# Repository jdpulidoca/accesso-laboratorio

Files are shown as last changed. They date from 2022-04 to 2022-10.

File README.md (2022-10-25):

# Proyecto Sistemas Embebidos 2022-1 : Control de Acceso para Laboratorios

## Brochure

<p align="center">
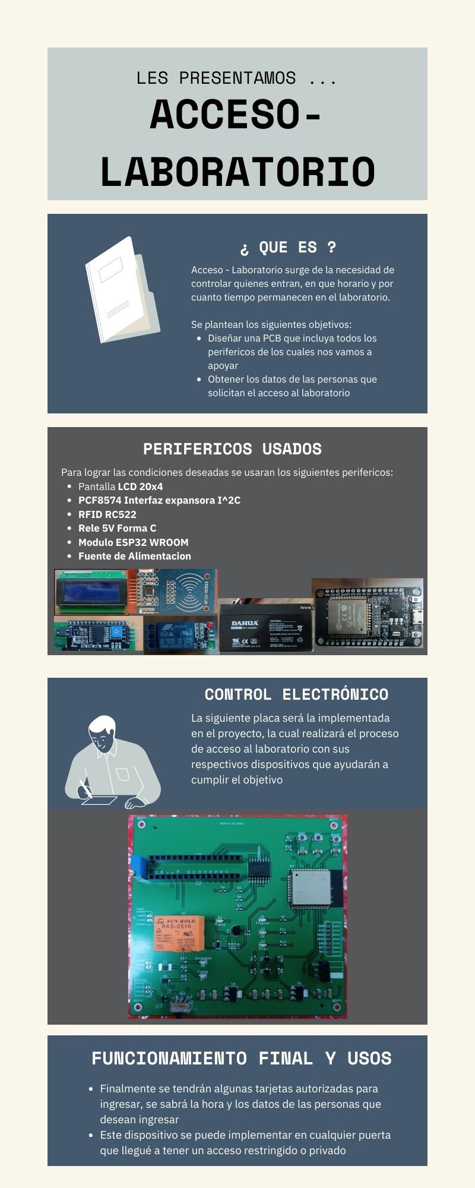
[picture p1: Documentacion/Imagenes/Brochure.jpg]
  
</p>

## Descripción
Como primer idea se plantea un sistema para acceder a un laboratoiro. Se tienen como condiciones que el acceso sea por medio del carnet universitario, donde al acercar el carnet al dispositivo que se diseñara, este desbloqueará la puerta y mostrara los datos en pantalla de la persona que desea ingresar al laboratorio. Este dispositivo activara y desactivara un electroiman que será el encargado de mantener la puerta bloqueada.

## Desarrollo y modelamiento

### Planteamiento Base del Diseño
Para lograr el objetivo del proyecto se plantean las primeras ideas en cuanto a diseño del dispositivo, se plantean las primeras ideas basicas en forma grafica con el fin de ordenar y establecer como  distribuir las tareas que corresponde a Hardware y Software. Esta ideacion esta sujeta a cambios o ajuste debido a las limitaciones del mismo.

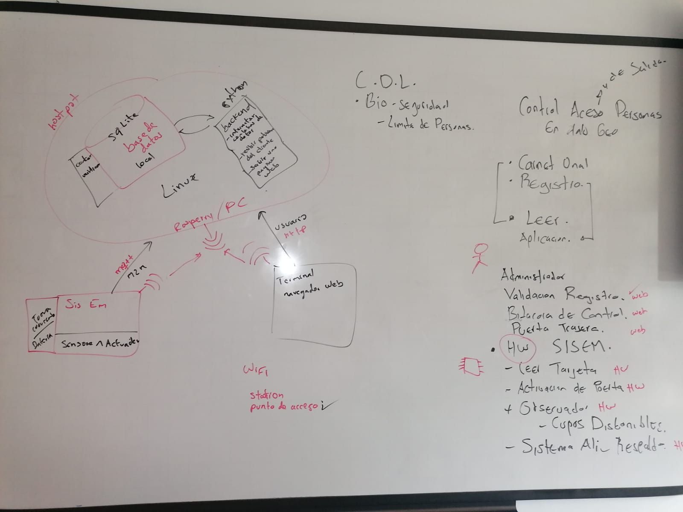
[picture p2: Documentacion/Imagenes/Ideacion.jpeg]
IdeasBasicas


### Diagrama de Bloques

<p align="center">
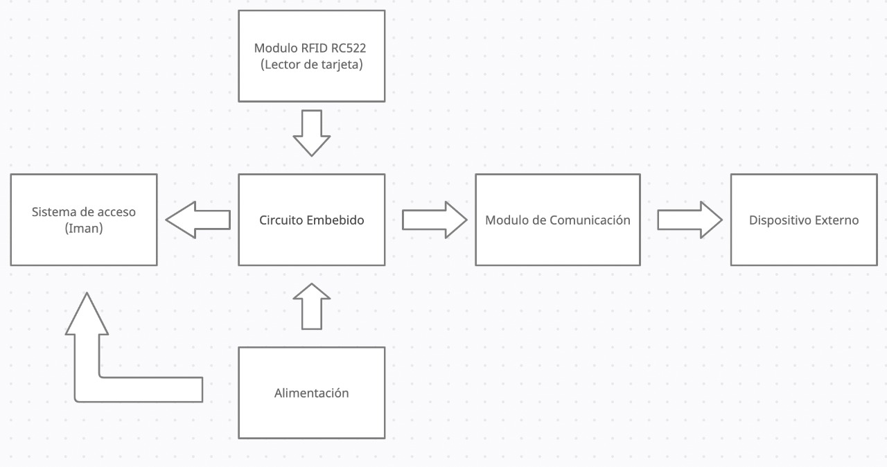
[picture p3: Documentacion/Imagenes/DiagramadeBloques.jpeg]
  
</p>

### Diagrama de Flujo

<p align="center">
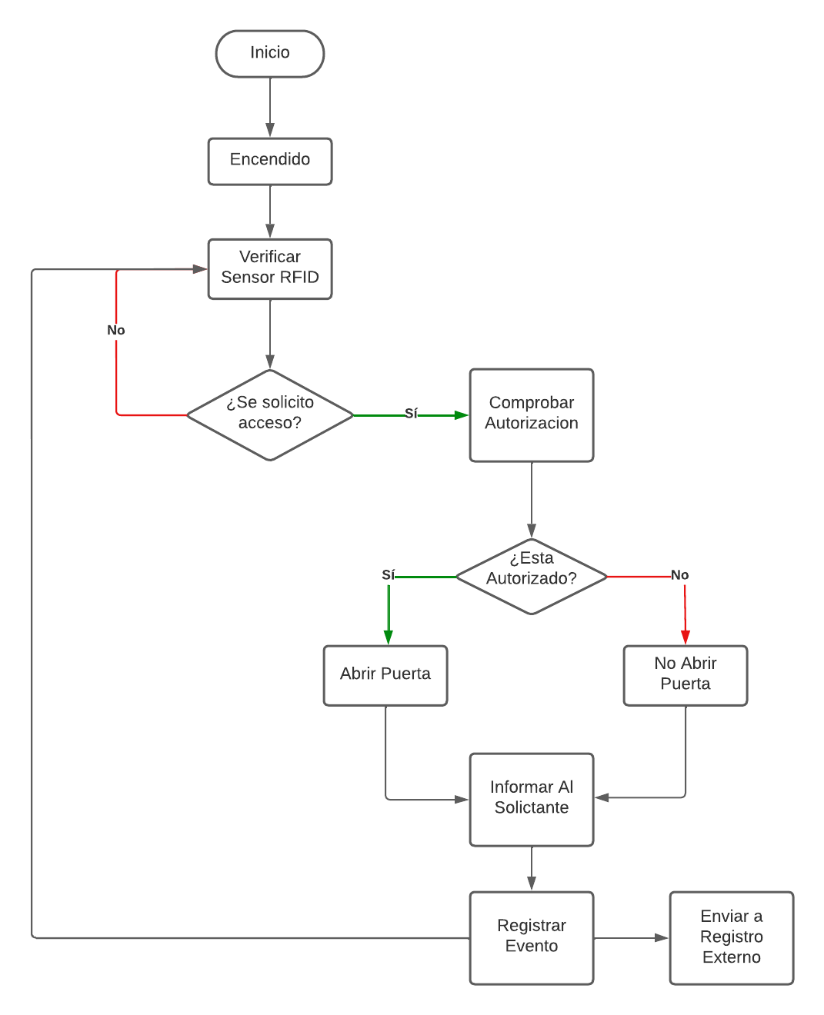
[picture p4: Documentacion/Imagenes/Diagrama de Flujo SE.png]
  
</p>

### Particionamiento Hardware y Software
#### HardWare
Para esta sección se establecen los siguientes periféricos:  
##### LCD 20x4
EL fin de este periferico es ver la información de la tarjeta con la que se desea ingresar, de igual manera ver si la solicitude de acceso al laboratoirio se aprueba o se denega.

<p align="center">
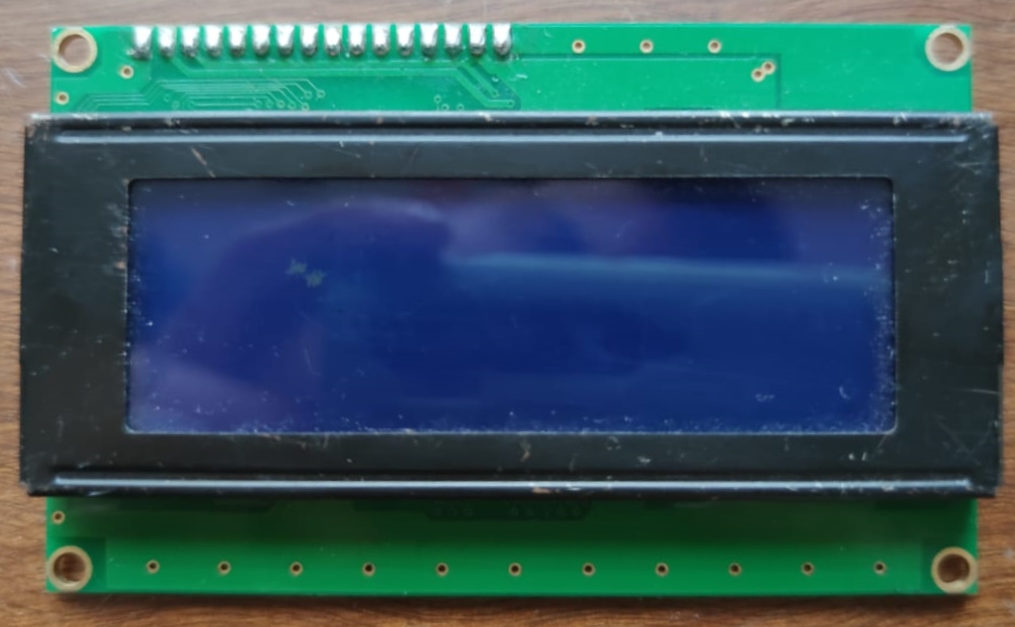
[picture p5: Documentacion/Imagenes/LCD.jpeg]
  
</p>

##### PCF8574 Interfaz expansora I^2C
Este modulo se estableció con el fin de generar una comunicación y así verificar los datos obtenidos por medio de la tarjeta entre el sistema implementado y un dispositivo externo.

<p align="center">
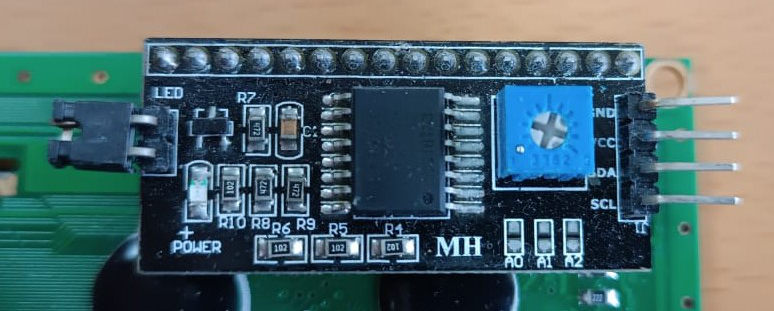
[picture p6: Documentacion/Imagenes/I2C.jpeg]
PCF8574
  
</p>

##### RFID RC522

Este modulo se implementa con el fin de leer los datos aportados por la tarjeta

<p align="center">
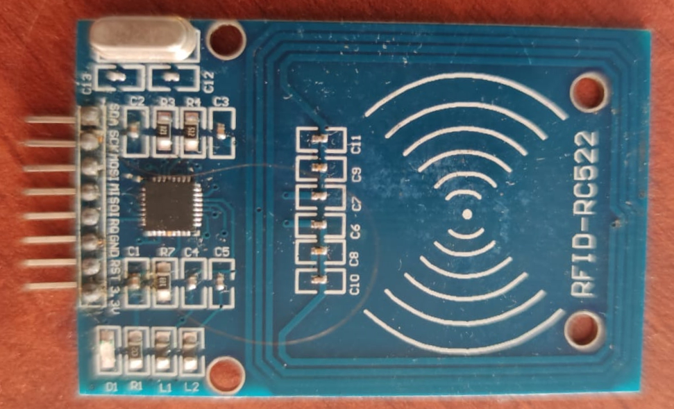
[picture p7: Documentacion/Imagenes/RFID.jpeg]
Sensor RFID-RC522
  
</p>

##### Rele 5V Forma C

Este modulo se implementa para aislar la señal digital que nos da o nos niega el acceso de la puerta

<p align="center">
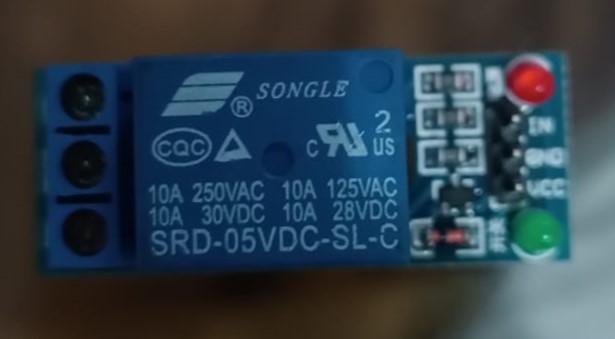
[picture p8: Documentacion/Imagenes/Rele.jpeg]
Modulo Rele 5V
  
</p>

##### Modulo ESP32 WROOM

Como último se tiene la tarjeta ESP32 desde donde se controlan los demás modulos, se implementa el codigo referente al proyecto

<p align="center">
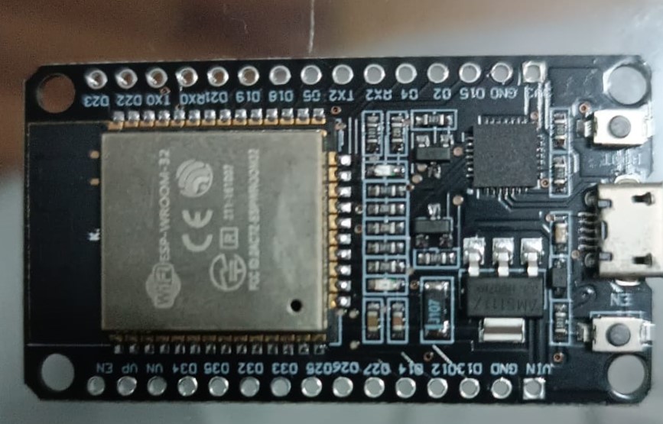
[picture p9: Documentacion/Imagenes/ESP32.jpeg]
Dev-Kit ESP32
  
</p>

##### Fuente de Alimentacion

Se plantean 2 soluciones para la alimentación del sistema, como primer solución se tiene una fuente variable que corresponde al de la siguiente imagen.

###### Fuente 12 V

<p align="center">
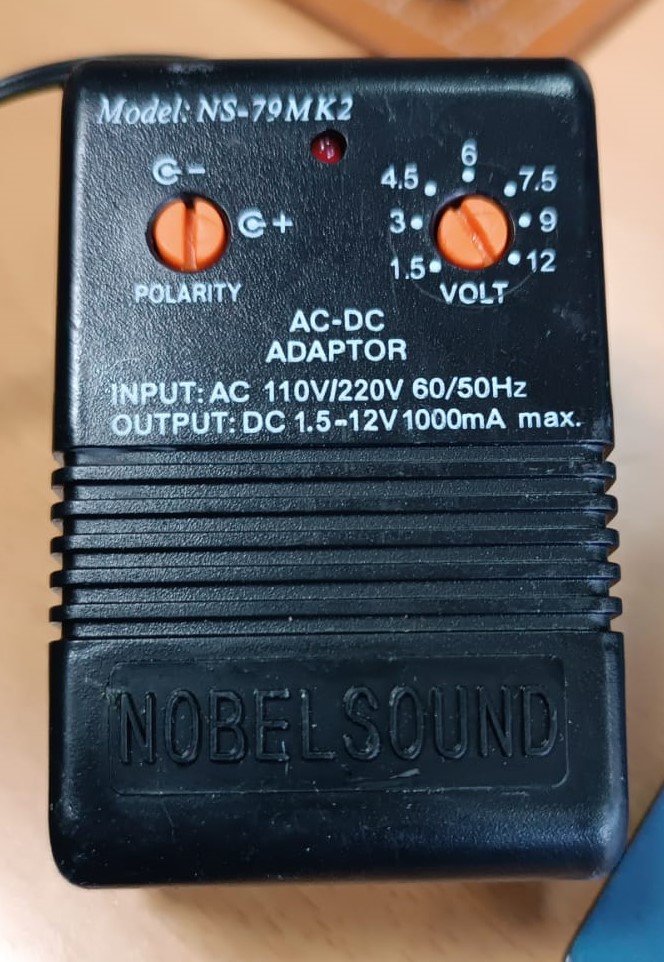
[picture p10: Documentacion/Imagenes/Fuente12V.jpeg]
Fuente12V
  
</p>

###### Bateria 12 V

Como segunda solución se plantea la implementación de una bateria extraida de una motocicleta, la cual se puede ver en la siguiente imagen

<p align="center">
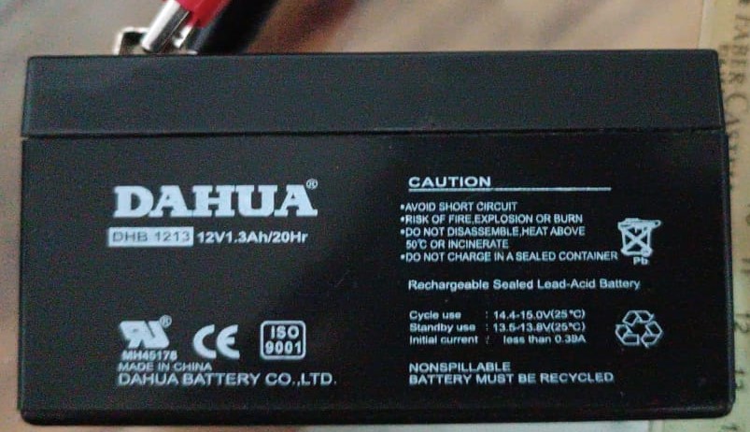
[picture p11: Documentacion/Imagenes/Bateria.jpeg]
Bateria 12 V
  
</p>

#### SoftWare
##### Codigo

### Esquema del Diseño

Este se divide en 4 "Islas" principales, divididos segun los valores de alimentacion. 

En primera instancia se se tienen los componetes que operan a con 3.3 V

En la siguiente imagen se muestra las conecciones a la ESP32, puertos de programación y adicional a esto tambien se puede evidenciar las conecciones del modulo RFID

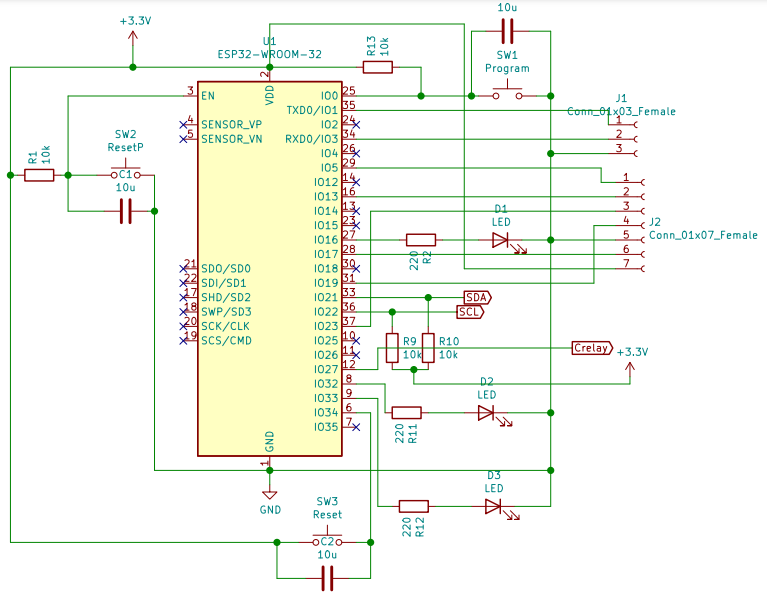
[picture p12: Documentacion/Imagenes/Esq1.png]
Esq1


Para la siguiente imagen se tienen las conecciones correspondientes a I2C para las pantallas LCD

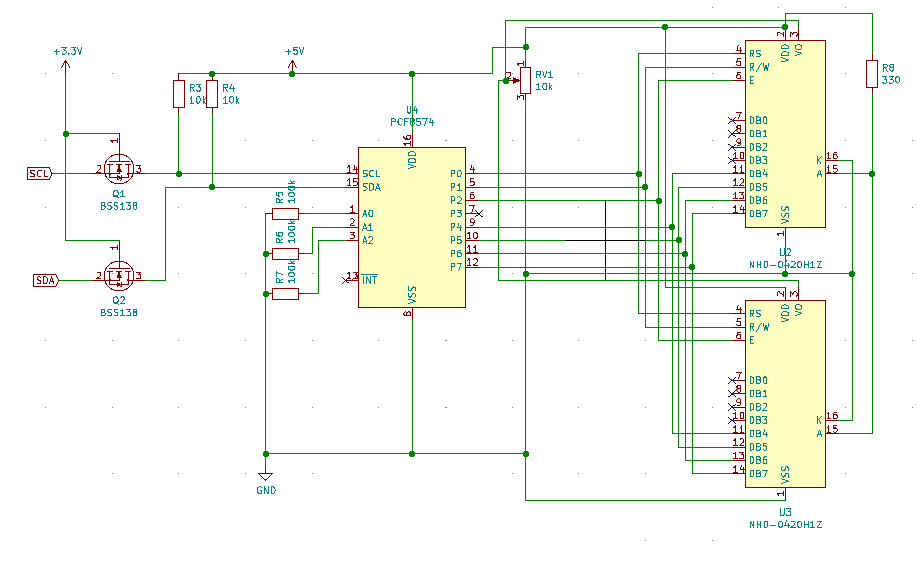
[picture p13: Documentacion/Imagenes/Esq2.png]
Esq2


Coneccion del rele con su respectivo controlador con el fin de activarlo con 3.3v y dar acceso al sistema

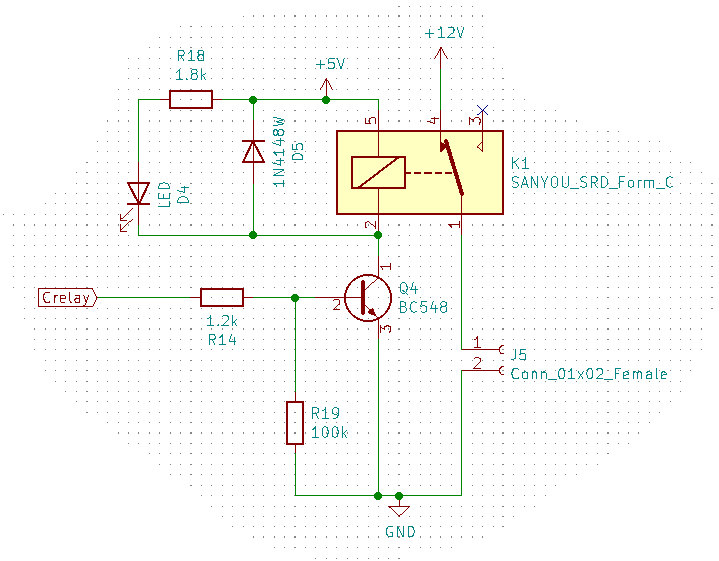
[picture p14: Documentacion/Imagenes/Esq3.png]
Esq3


Y por ultimo tenemos un sistema de fuentes lineales con el cual podemos reducir la tensión de 12v a 5v y de 5v a 3.3. Este mismo cambio de fuente a bateria en caso de una interrupción en la alimentación

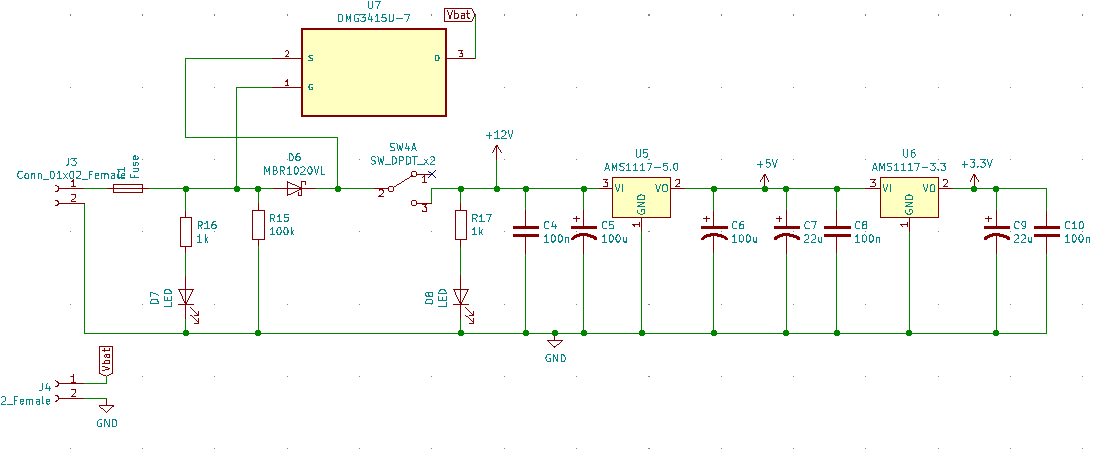
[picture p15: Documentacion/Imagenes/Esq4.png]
Esq4


### Diseño del Circuito Impreso

Se muestra el prototipo que se obtendra al imprimir la tarjeta y los dispositivos a soldar

<p align="center">
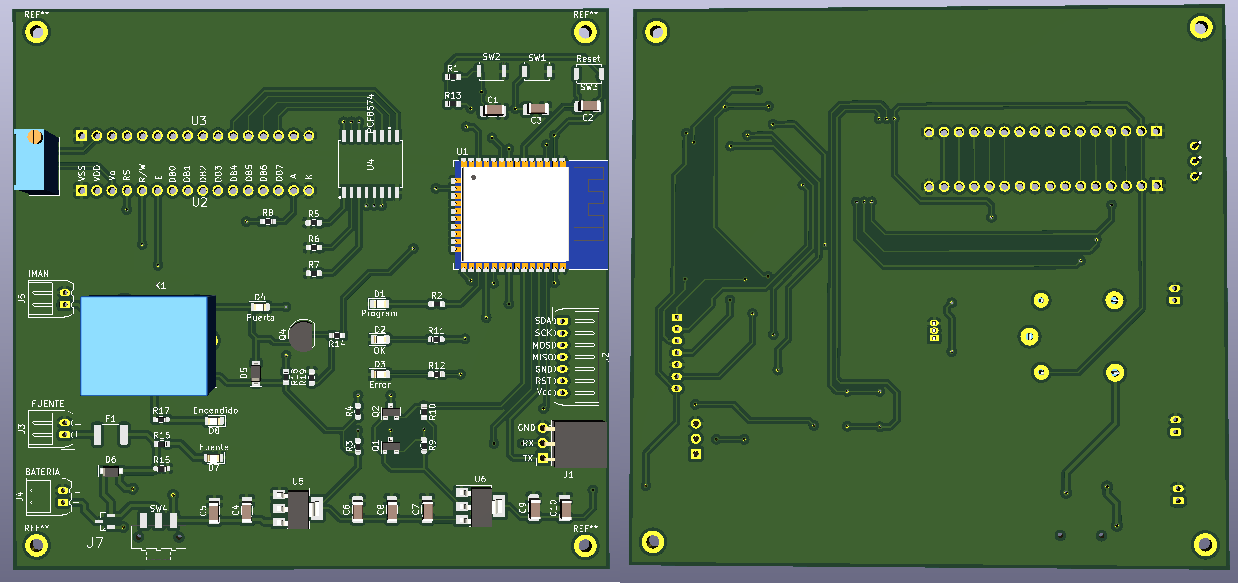
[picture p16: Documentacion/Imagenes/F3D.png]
  
</p>

### Error de Diseño
### Proceso de Compra

Despues de terminar el diseño de la PCB se empieza a estuiar los posibles proveedores para mandar imprimir dicha placa, con lo que se decide mandarla imprimir en JLCPBC

<p align="center">
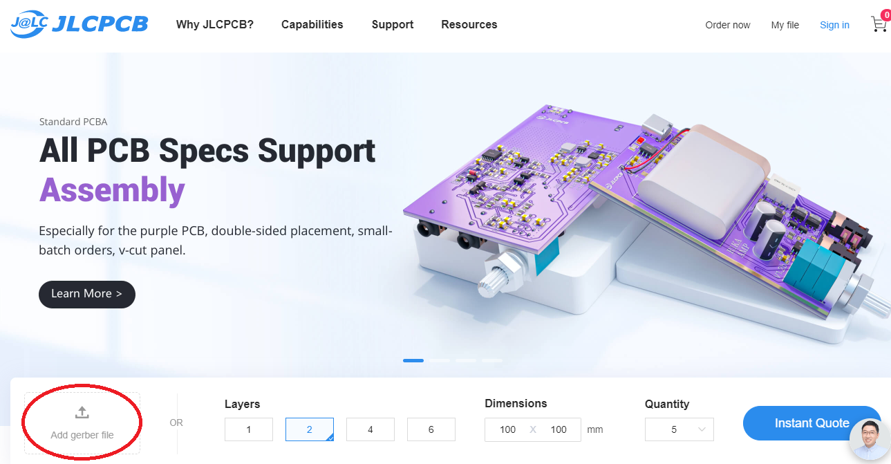
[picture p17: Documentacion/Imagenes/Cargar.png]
  
</p>

Seguido a esto se carga el diseño y se confirma la compra, la compra se realiza con tarjeta de debito.

En las siguientes imagenes se observara el proceso de compra paso a paso

Se seleccionan las diferentes caracteristicas referentes a la PCB y a los datos de envio, tambien se evidencian los costos e impuestos adicionales que no se tenían previstos.
<p align="center">
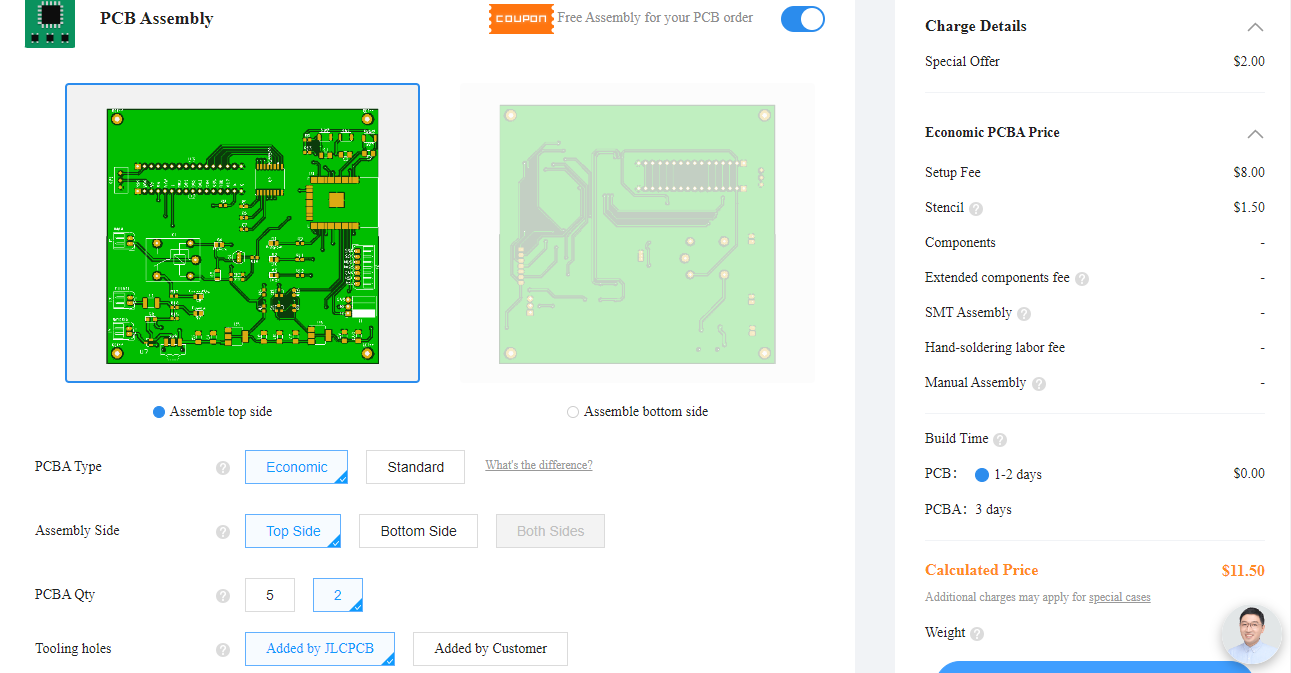
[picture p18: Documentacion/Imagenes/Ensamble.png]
  
</p>

Datos de envio
<p align="center">
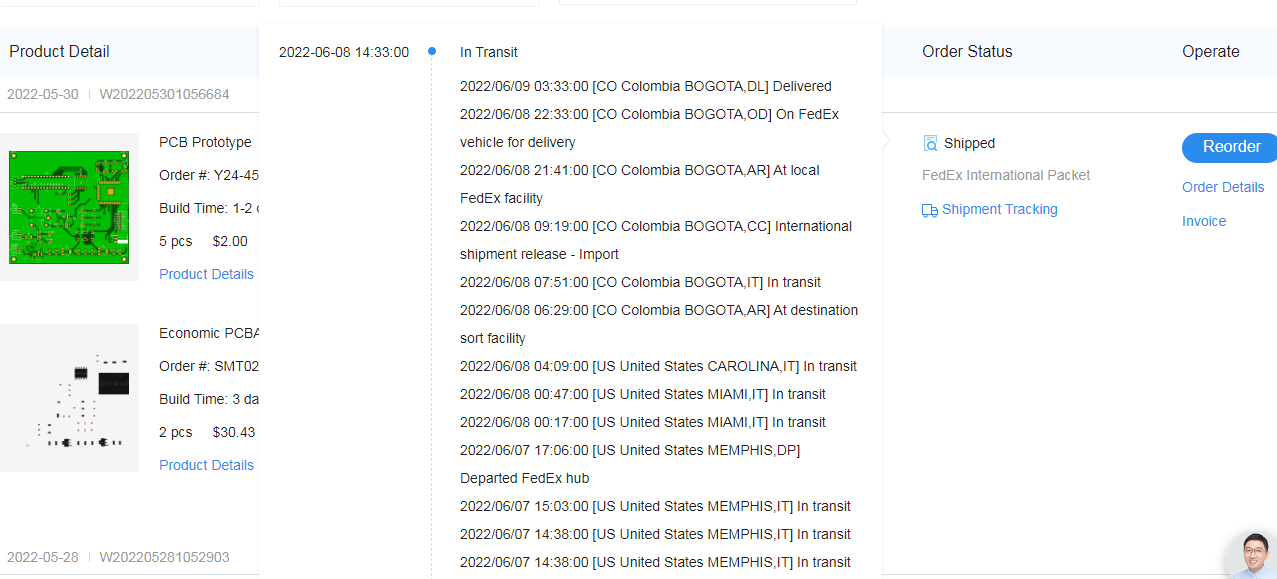
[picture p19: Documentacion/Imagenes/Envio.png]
  
</p>

Valor estimado

<p align="center">
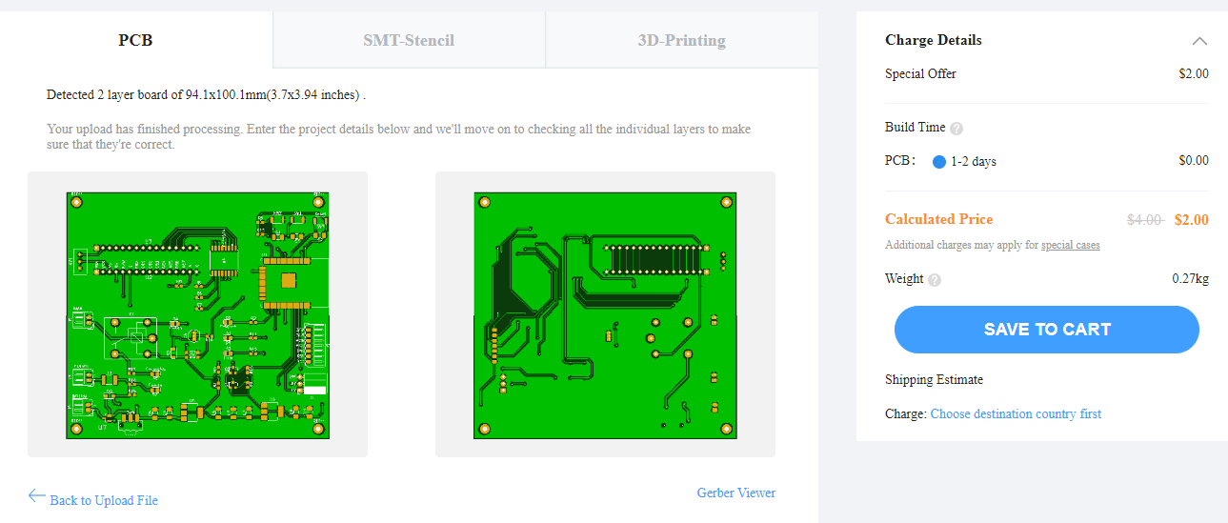
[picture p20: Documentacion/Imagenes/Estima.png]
  
</p>

Se modifica el archivo de elementos que se solicitaron soldar ya que la pagina solicitaba un formato especifico para poder ser procesado. Adicional a esto se escogen los dispositivos donde se tratan de adecuar a la necesidad del proyecto y al presupuesto

<p align="center">
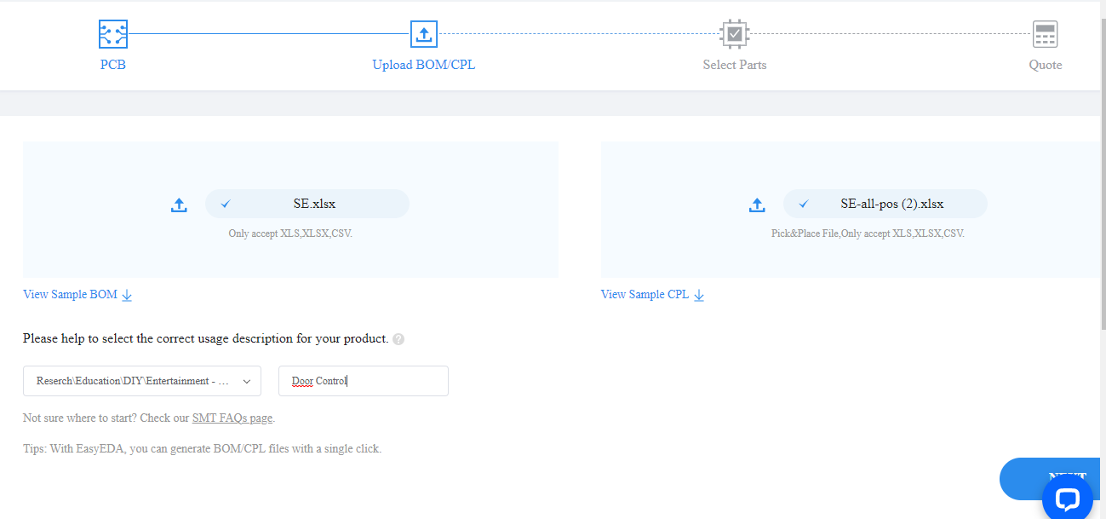
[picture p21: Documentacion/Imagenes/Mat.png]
  
</p>

<p align="center">
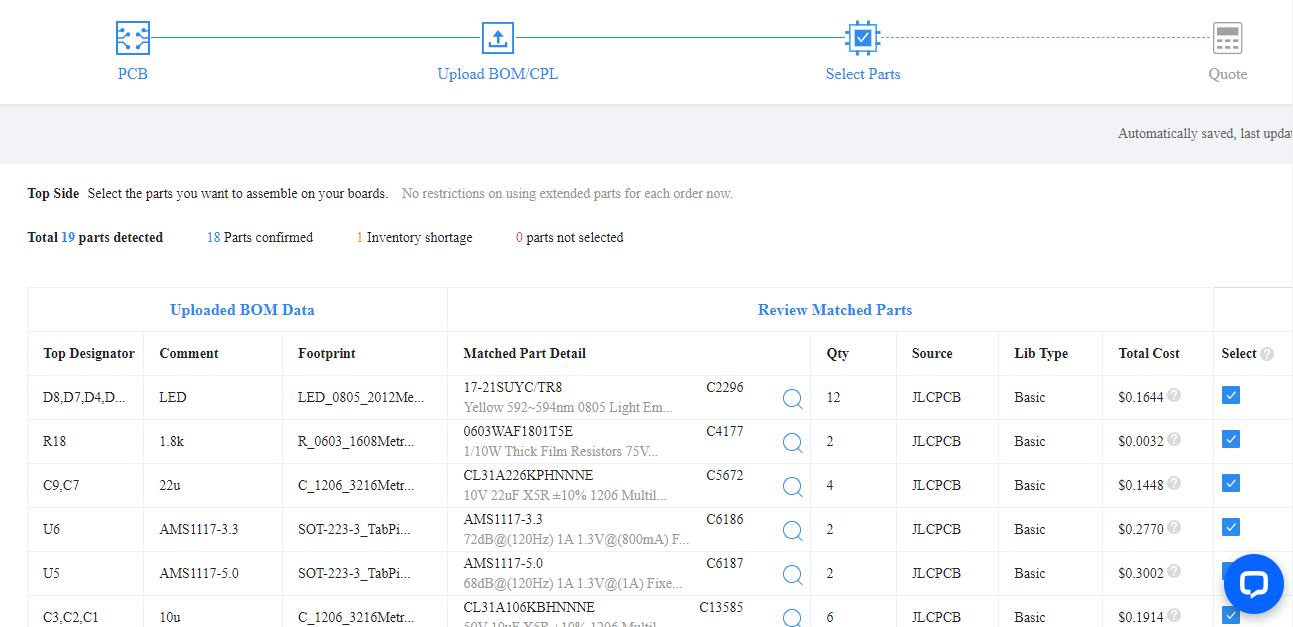
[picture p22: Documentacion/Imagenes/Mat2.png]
  
</p>

<p align="center">
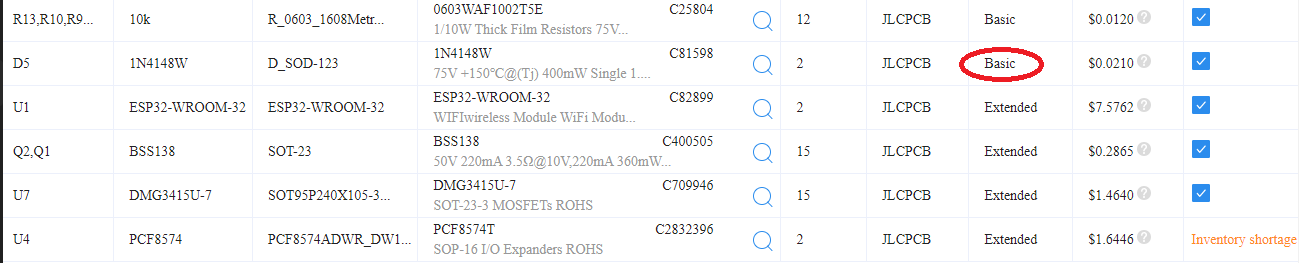
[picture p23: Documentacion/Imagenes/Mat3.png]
  
</p>

Se adjunta evidencia del proceso de compra

<p align="center">
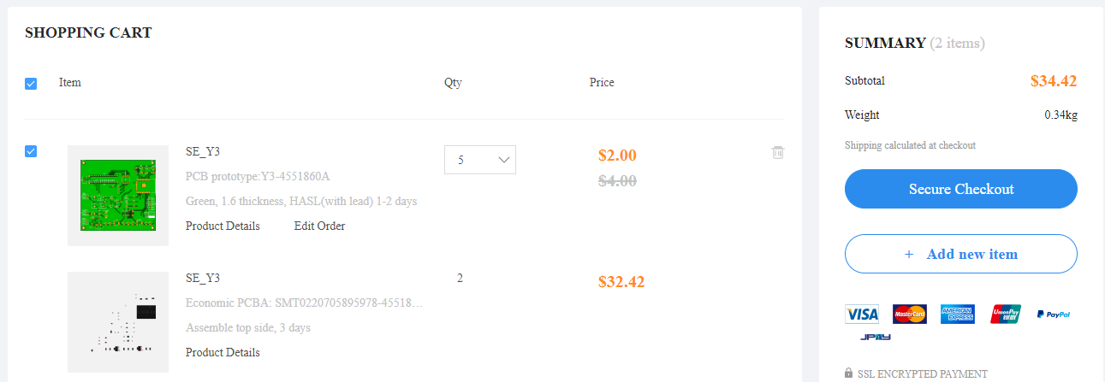
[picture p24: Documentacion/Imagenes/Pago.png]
  
</p>
<p align="center">
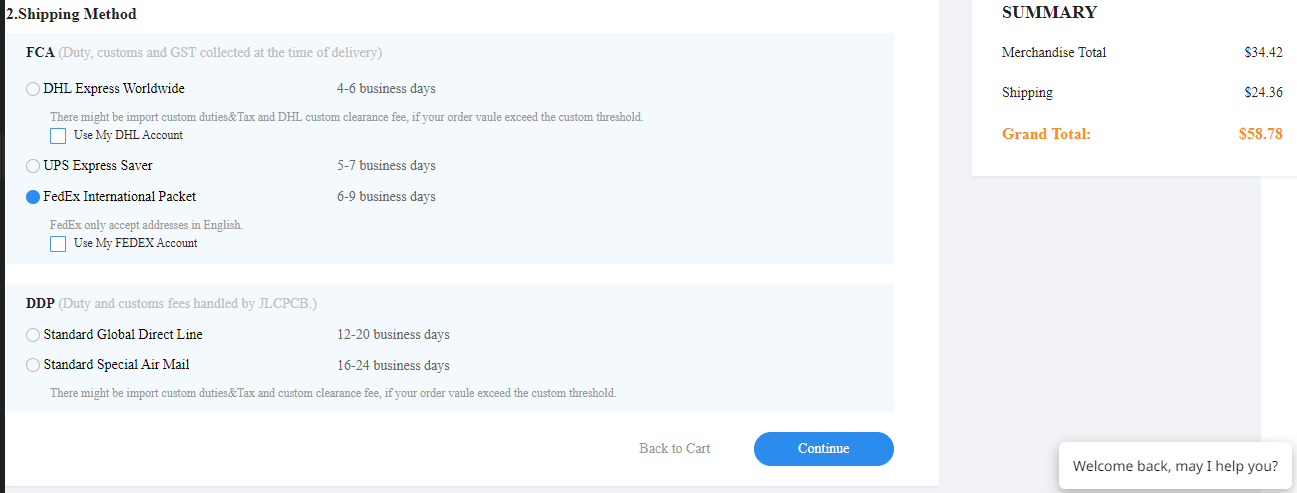
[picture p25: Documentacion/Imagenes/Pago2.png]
  
</p>

<p align="center">
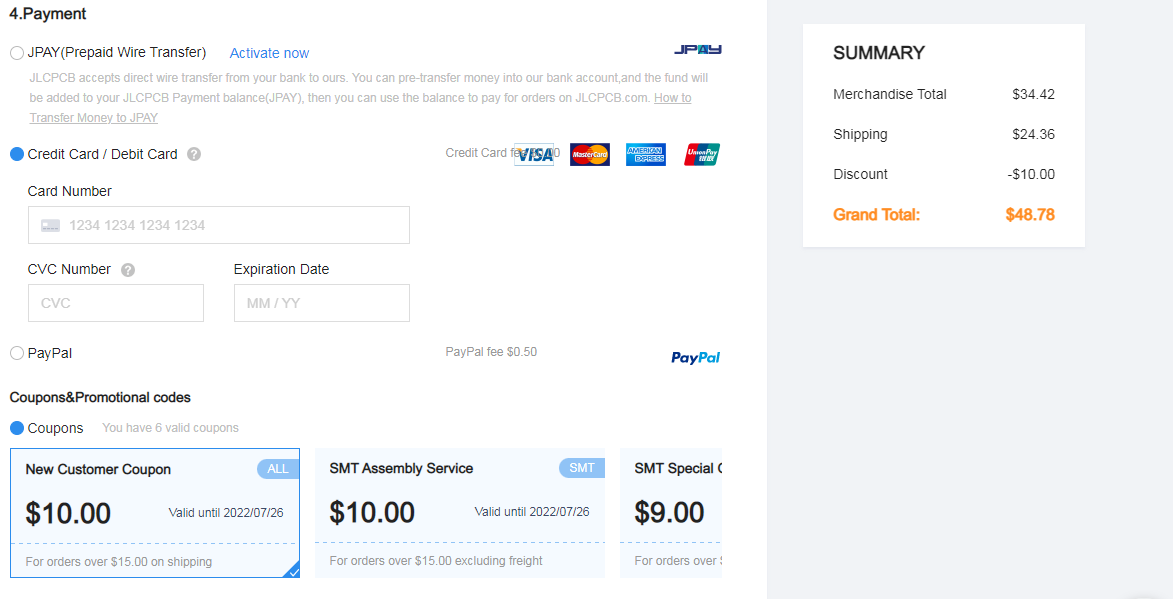
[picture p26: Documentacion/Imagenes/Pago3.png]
  
</p>

Se muestra la factura del impuesto adicional que toca pagar al llegar el paquete. este impuesto se entiende como un proceso de nacionalización del producto ya que Colombia no posee tratado de libre comercio con china.

<p align="center">
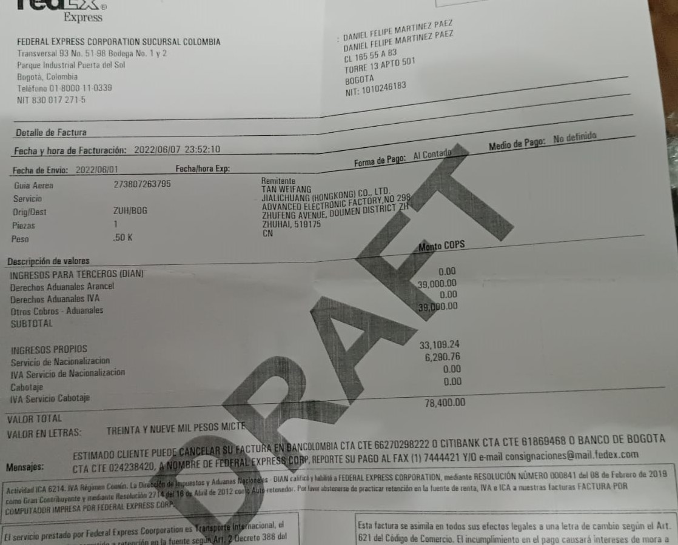
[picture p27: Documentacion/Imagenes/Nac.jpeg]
  
</p>

<p align="center">
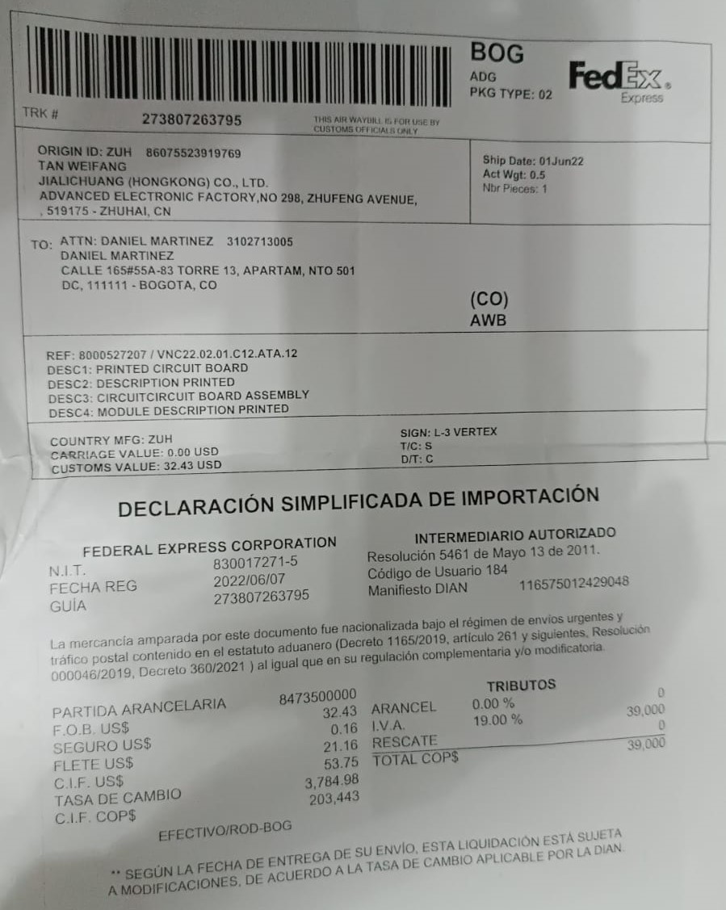
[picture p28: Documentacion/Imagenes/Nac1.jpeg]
  
</p>

## Pruebas
Las pruebas se realizaron sobre 2 tajetas. En primer lugar se trabajo con una tarjeta  experimental, que consiste en una baquelita solda donde se probaron los perifericos mediantes una tarjeta de desarrollo ESP32 DEVKIT V1. Una vez comprobado el funcionamiento de los perifericos y el codigo en la tarjeta experimental, se procede a aplicarlo en la PCB diseñada y realizar los cambios pertinentes para lograr las tares que se requieren.
### Experimental

Primero se prueban cada uno de los perifericos con el fin de verificar que esten en buen estado como se muestran en las siguientes imagenes

Empezamos adecuando un ESP32 para hacer las pruebas
<p align="center">
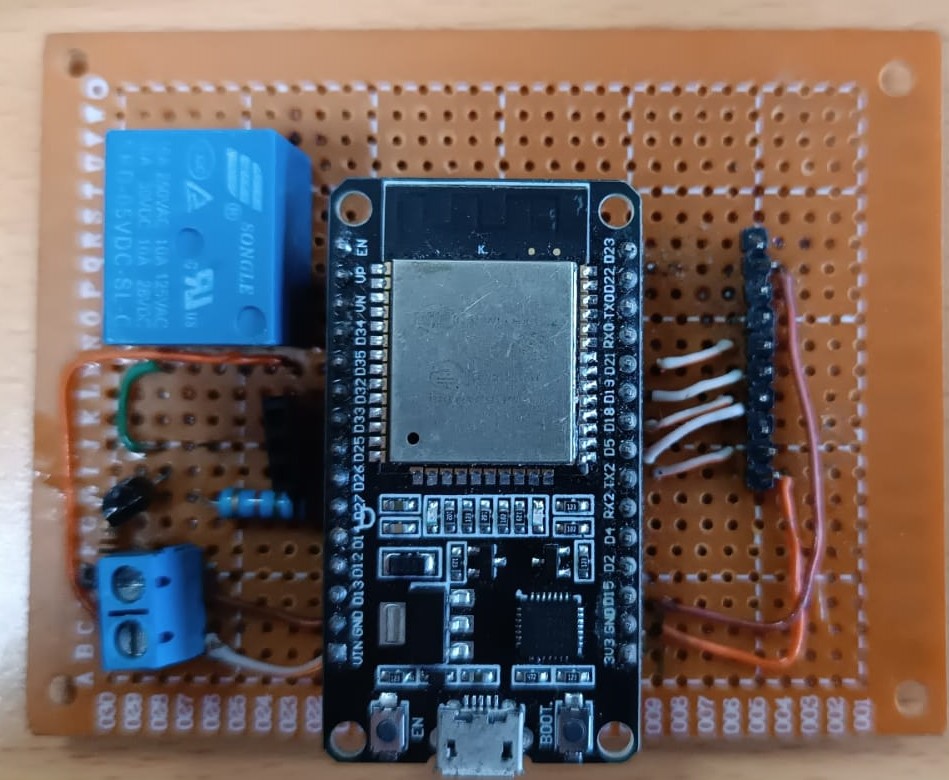
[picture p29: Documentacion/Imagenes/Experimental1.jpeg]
Tarjeta EXperimental
  
</p>
<p align="center">
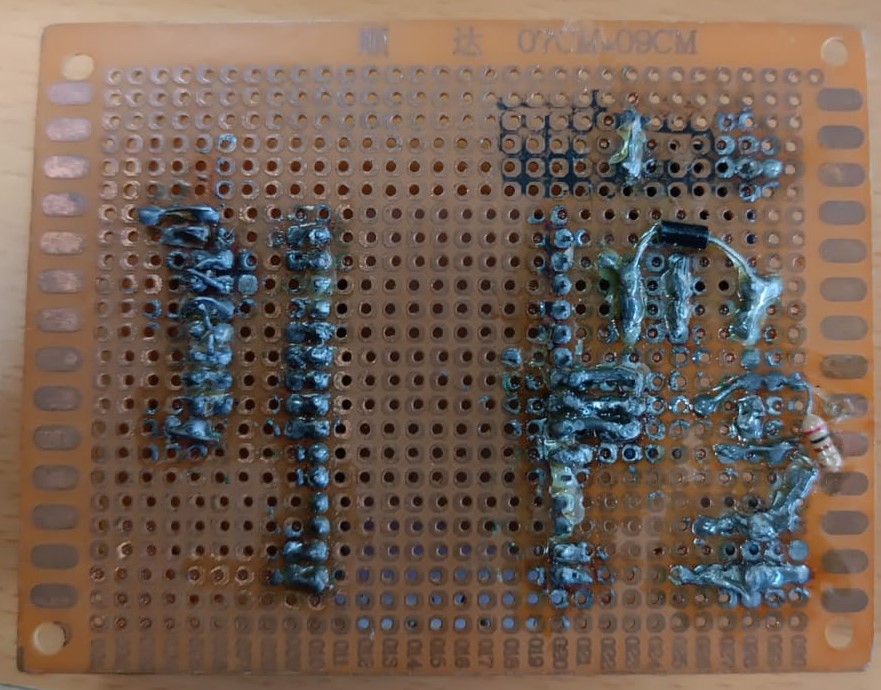
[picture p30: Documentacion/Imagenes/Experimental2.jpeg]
Tarjeta EXperimental
  
</p>

Seguido a esto probamos el modulo RFID

<p align="center">
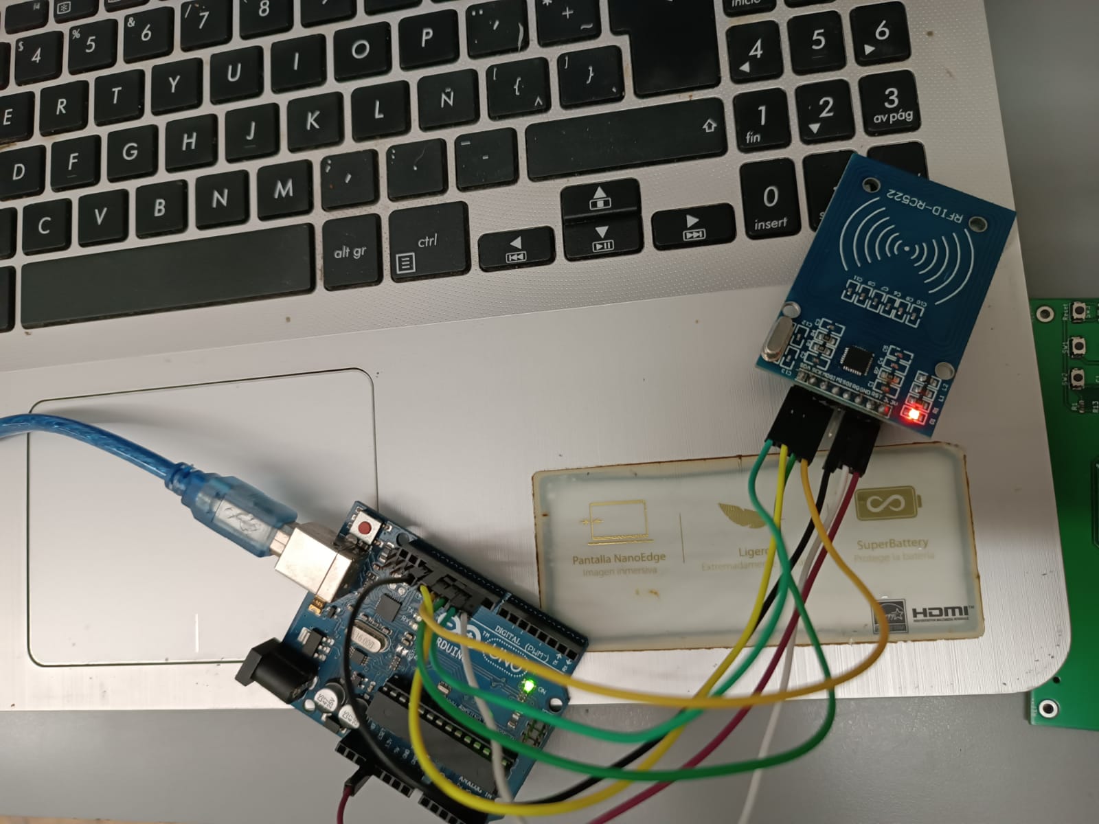
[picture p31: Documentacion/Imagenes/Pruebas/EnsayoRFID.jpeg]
  
</p>

Pruebas en bateria y fuente

<p align="center">
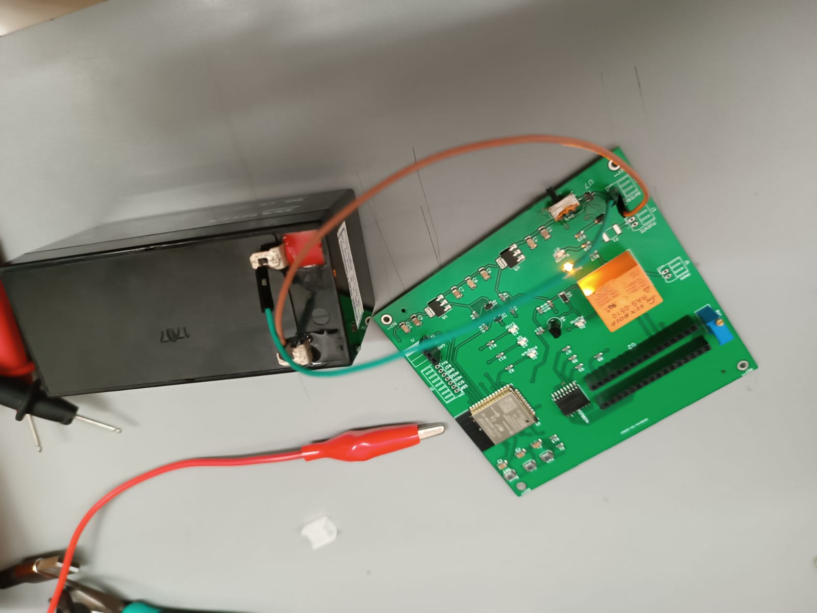
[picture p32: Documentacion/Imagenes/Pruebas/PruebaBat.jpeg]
  
</p>

<p align="center">
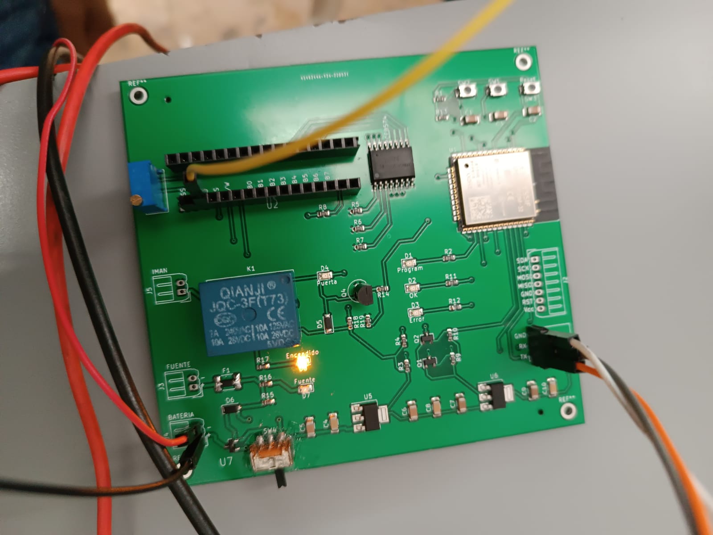
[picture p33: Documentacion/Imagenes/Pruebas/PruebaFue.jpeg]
  
</p>

Se conectan los modulos RFID y la pantalla LCD

<p align="center">
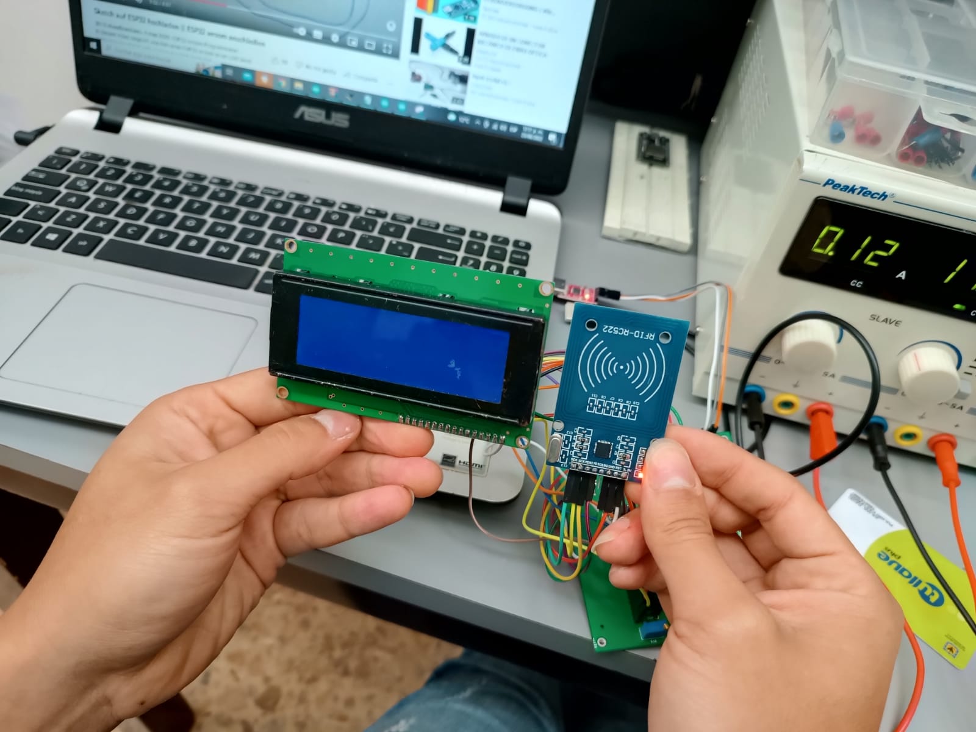
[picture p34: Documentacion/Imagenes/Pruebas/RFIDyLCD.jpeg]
  
</p>

<p align="center">
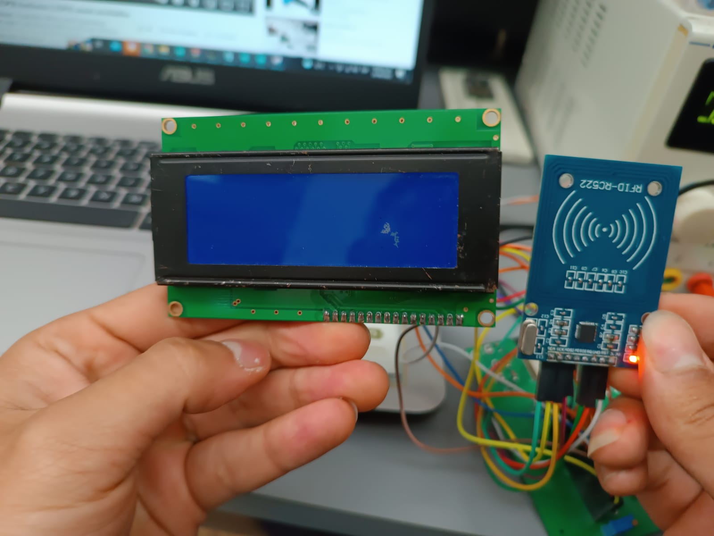
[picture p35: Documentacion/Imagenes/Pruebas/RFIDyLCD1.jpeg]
  
</p>

### Diseñada

<p align="center">
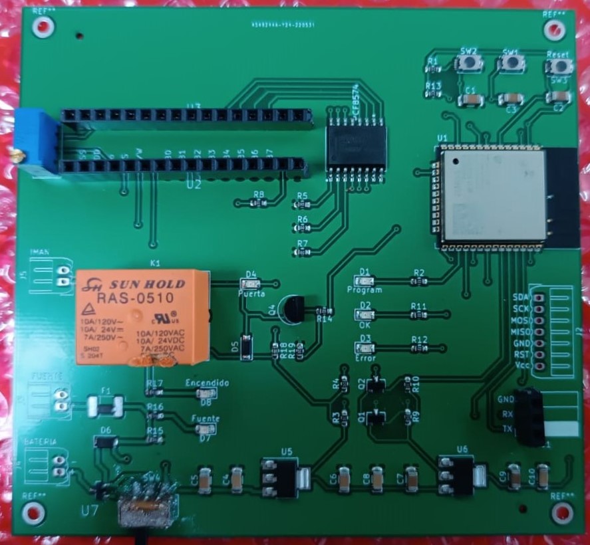
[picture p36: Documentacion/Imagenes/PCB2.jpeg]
  
</p>
<p align="center">
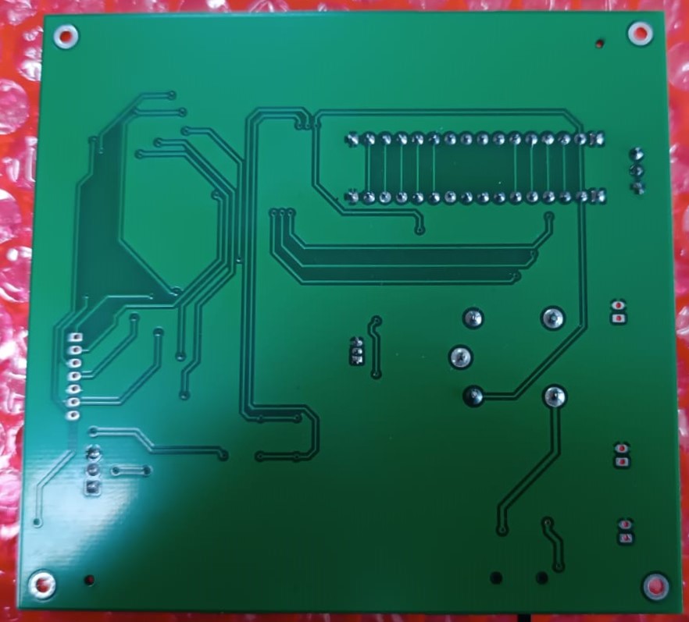
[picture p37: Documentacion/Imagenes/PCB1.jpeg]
  
</p>

## Funcionamiento

Al conectar los diferentes perifericos junto a la PCB se tiene que al acercar una tarjeta autorizada los datos de la tarjeta llegarán a la pantalla y el dispositivo dará acceso de entrada a la puerta. Por otro lado, cuando se acerque una tarjeta no autorizada igualmente se tendrán los datos en pantalla junto al mensaje de acceso denegado, pero en esta ocasión no se dará acceso a la puerta.

## Resultados

Como resultados a las pruebas se realizaron diferentes pruebas.

La primer prueba realizada para probar el modulo RFID, donde se identifica que se han podido leer los datos de las tarjetas y se evidencia que se tiene la respuesta segun dado el nivel de acceso de latrjeta. Se grabaron los siguientes videos:

(https://www.youtube.com/watch?v=JyA0l8uYjHc)

(https://www.youtube.com/watch?v=KVfLOUL_9iw)

Despues de haber implementado los diferentes modulos se realizan las siguientes pruebas y se mostraran los resultados obtenidos

(https://www.youtube.com/watch?v=XaRdIia-tdM)

(https://www.youtube.com/watch?v=Qwj3iA4QY8g)

### Prototipo

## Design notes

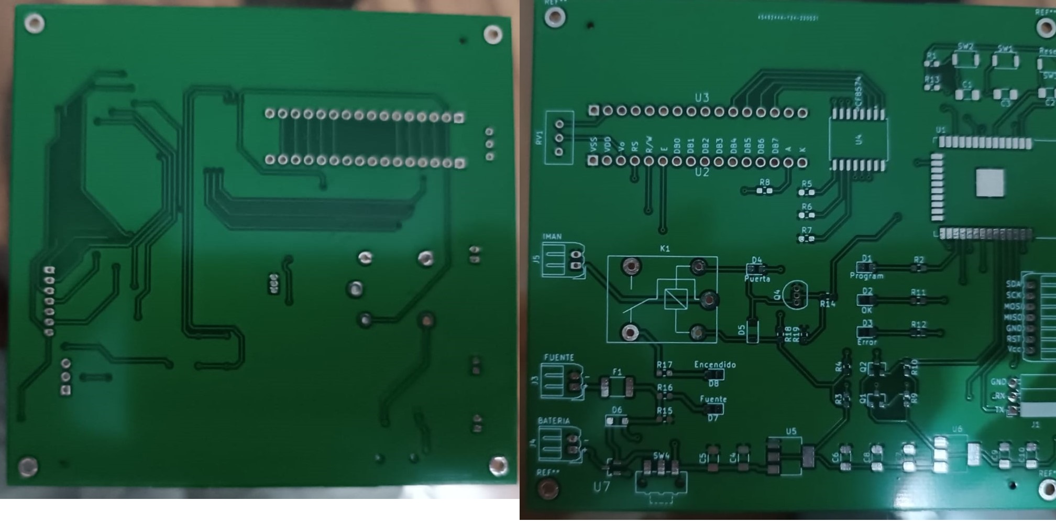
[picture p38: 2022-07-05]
Documentacion/Imagenes/PCB3.jpeg

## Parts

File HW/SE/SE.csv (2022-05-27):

Id | Identificador | Empaquetado | Cantidad | Identificación | Suministrador y ref
1 | D8,D7,D4,D3,D2,D1 | LED_0805_2012Metric_Pad1.15x1.40mm_HandSolder | 6 | LED
2 | C10,C8,C4 | C_1206_3216Metric_Pad1.33x1.80mm_HandSolder | 3 | 100n
3 | C9,C7 | C_1206_3216Metric_Pad1.33x1.80mm_HandSolder | 2 | 22u
4 | C6,C5 | C_1206_3216Metric_Pad1.33x1.80mm_HandSolder | 2 | 100u
5 | C3,C2,C1 | C_1206_3216Metric_Pad1.33x1.80mm_HandSolder | 3 | 10u
6 | REF**,REF**,REF**,REF** | MountingHole_2.2mm_M2_ISO14580_Pad | 4 | MountingHole_2.2mm_M2_ISO14580_Pad
7 | U2,U3 | LCD_LCD-20X4B | 2 | NHD-0420H1Z
8 | U7 | SOT95P240X105-3N | 1 | DMG3415U-7
9 | U6 | SOT-223-3_TabPin2 | 1 | AMS1117-3.3
10 | U5 | SOT-223-3_TabPin2 | 1 | AMS1117-5.0
11 | U4 | PCF8574ADWR_DW16 | 1 | PCF8574
12 | U1 | ESP32-WROOM-32 | 1 | ESP32-WROOM-32
13 | SW4 | SW_SPDT_CK-JS102011SAQN | 1 | SW_DPDT_x2
14 | SW3 | SW_Push_SPST_NO_Alps_SKRK | 1 | Reset
15 | SW2 | SW_Push_SPST_NO_Alps_SKRK | 1 | ResetP
16 | SW1 | SW_Push_SPST_NO_Alps_SKRK | 1 | Program
17 | RV1 | Potentiometer_Bourns_3296W_Vertical | 1 | 10k
18 | R19,R15,R7,R6,R5 | R_0603_1608Metric_Pad0.98x0.95mm_HandSolder | 5 | 100k
19 | R18 | R_0603_1608Metric_Pad0.98x0.95mm_HandSolder | 1 | 1.8k
20 | R17,R16 | R_0603_1608Metric_Pad0.98x0.95mm_HandSolder | 2 | 1k
21 | R14 | R_0603_1608Metric_Pad0.98x0.95mm_HandSolder | 1 | 1.2k
22 | R13,R10,R9,R4,R3,R1 | R_0603_1608Metric_Pad0.98x0.95mm_HandSolder | 6 | 10k
23 | R12,R11,R2 | R_0603_1608Metric_Pad0.98x0.95mm_HandSolder | 3 | 220
24 | R8 | R_0603_1608Metric_Pad0.98x0.95mm_HandSolder | 1 | 330
25 | Q4 | TO-92_Inline | 1 | BC548
26 | Q2,Q1 | SOT-23 | 2 | BSS138
27 | K1 | Relay_SPDT_SANYOU_SRD_Series_Form_C | 1 | SANYOU_SRD_Form_C
28 | J5,J4,J3 | Molex_Micro-Latch_53254-0270_1x02_P2.00mm_Horizontal | 3 | Conn_01x02_Female
29 | J2 | Molex_Micro-Latch_53254-0770_1x07_P2.00mm_Horizontal | 1 | Conn_01x07_Female
30 | J1 | PinSocket_1x03_P2.54mm_Horizontal | 1 | Conn_01x03_Female
31 | F1 | Fuse_1812_4532Metric_Pad1.30x3.40mm_HandSolder | 1 | Fuse
32 | D6 | D_SOD-123F | 1 | MBR1020VL
33 | D5 | D_SOD-123 | 1 | 1N4148W

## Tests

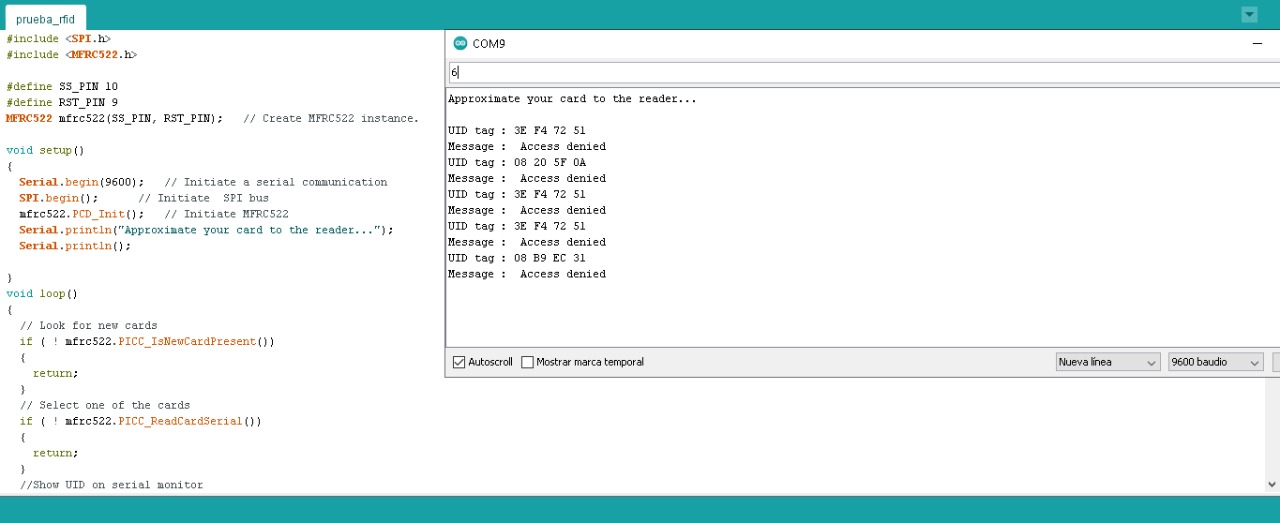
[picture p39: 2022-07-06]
Documentacion/Imagenes/Pruebas/Protoboard RFID.jpeg

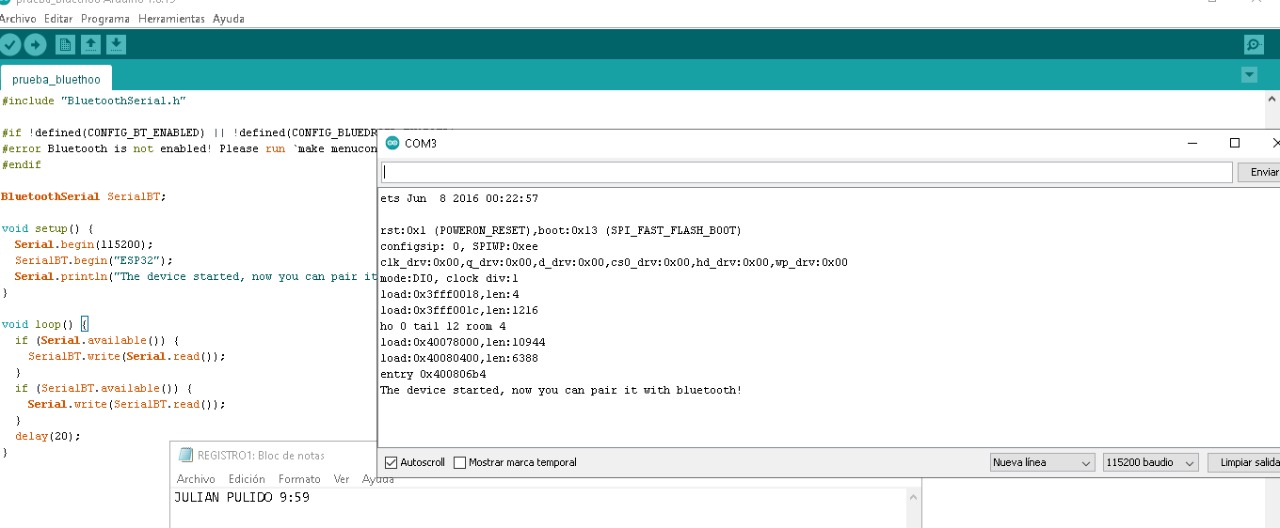
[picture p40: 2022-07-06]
Documentacion/Imagenes/Pruebas/PCB BlueTooth.jpeg

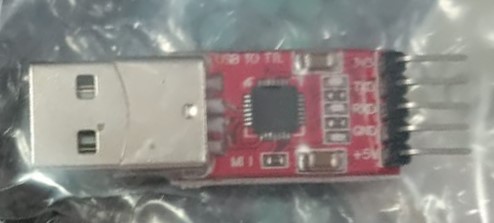
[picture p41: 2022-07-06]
Documentacion/Imagenes/Pruebas/RS232 UART.jpeg

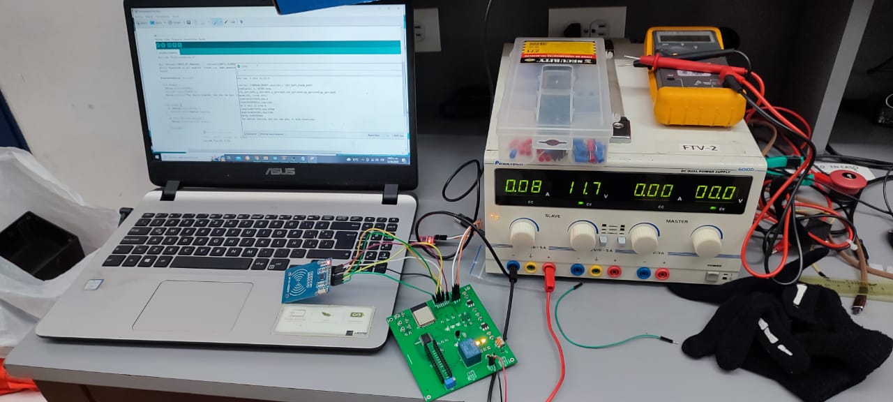
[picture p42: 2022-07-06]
Documentacion/Imagenes/Pruebas/PCB Fuente Externa y RFID.jpeg

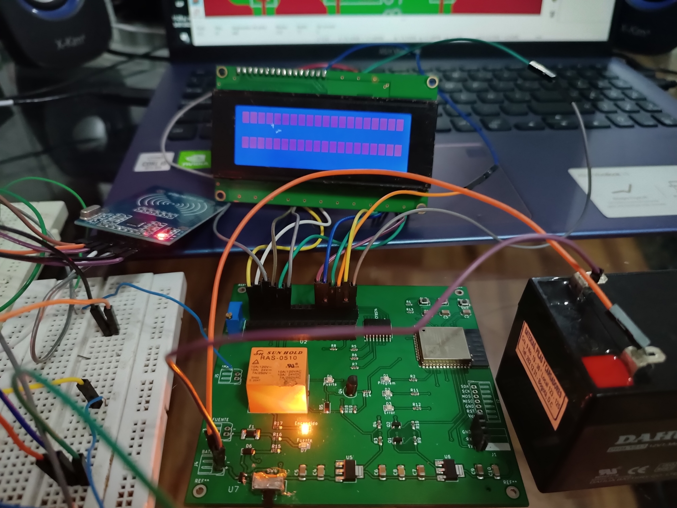
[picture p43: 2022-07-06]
Documentacion/Imagenes/Pruebas/Truncamiento LCD.jpg

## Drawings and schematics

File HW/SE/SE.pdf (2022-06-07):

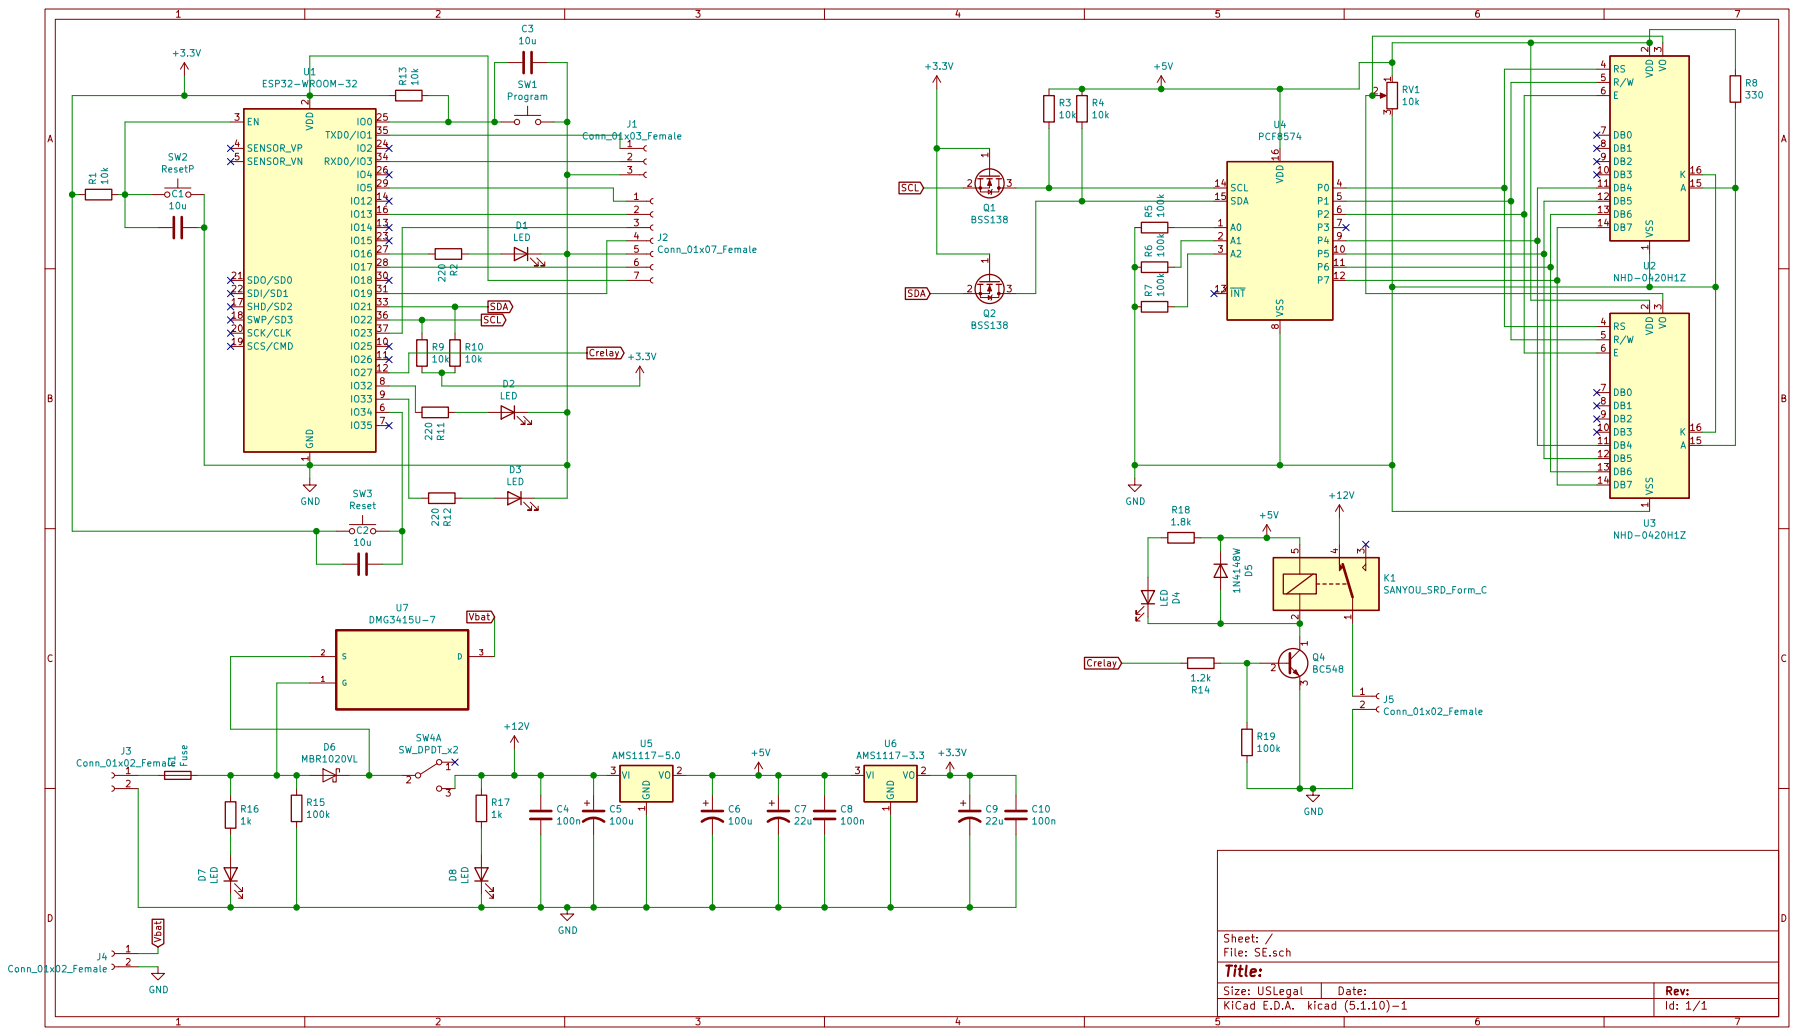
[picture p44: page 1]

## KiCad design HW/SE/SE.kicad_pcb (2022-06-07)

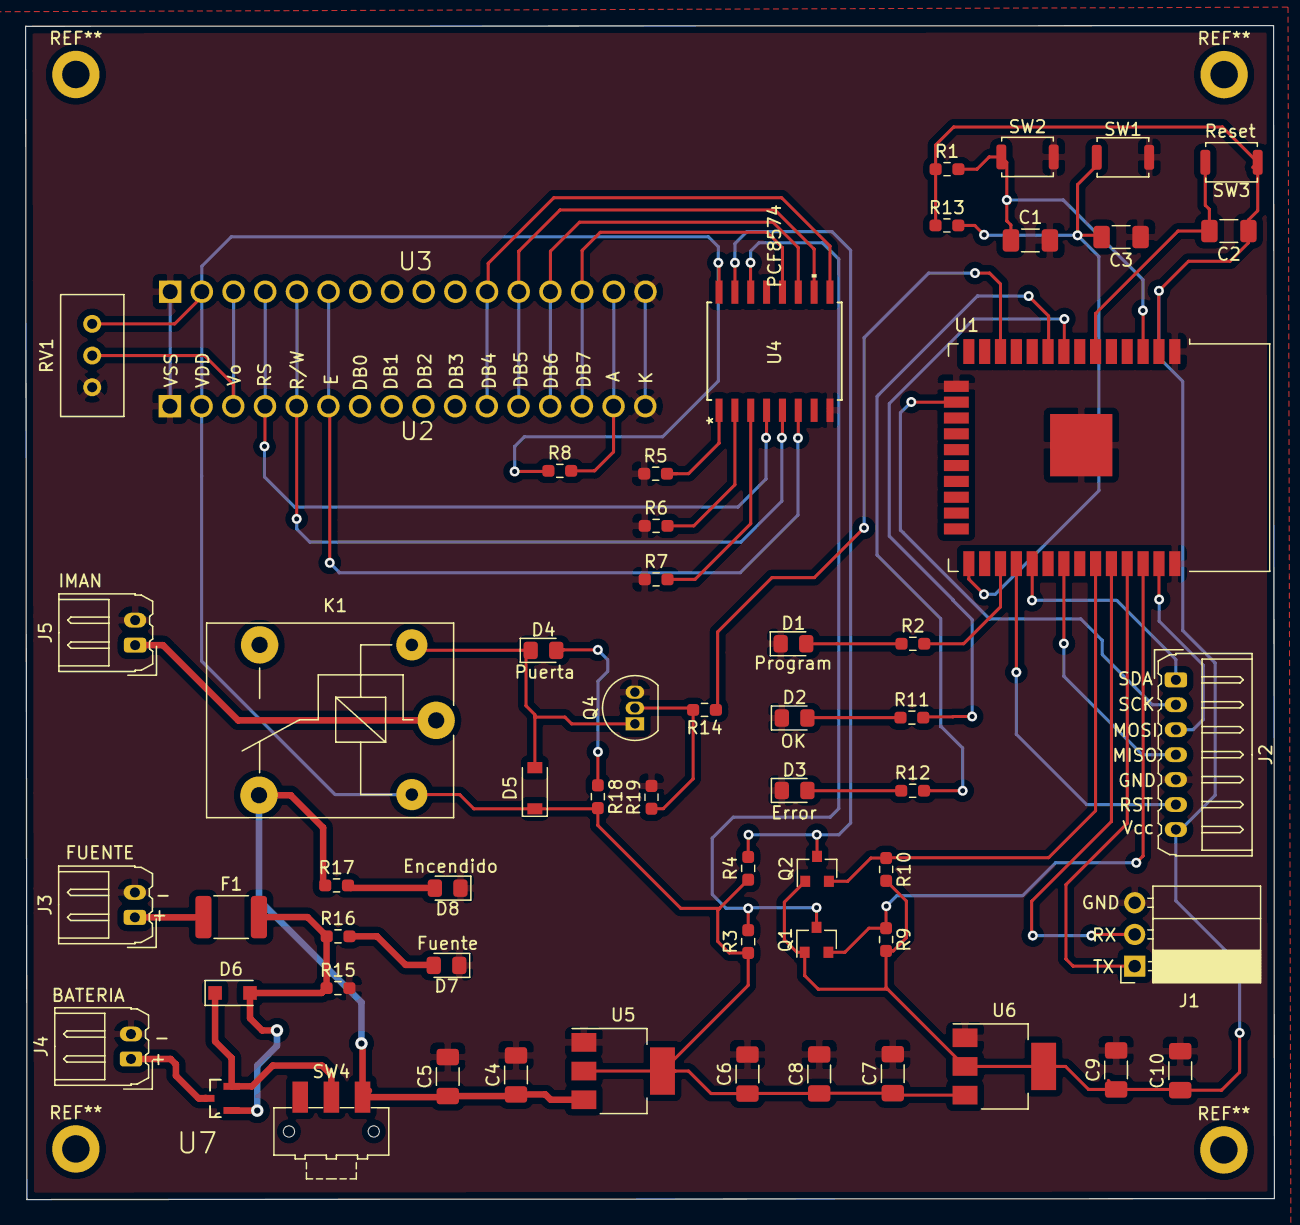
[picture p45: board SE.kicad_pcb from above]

Board: 2 copper layers, 100.1 x 94.1 mm, 59 parts (0 on the bottom side), 47 nets.

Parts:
C1, C2, C3: 10u; C_1206_3216Metric_Pad1.33x1.80mm_HandSolder
C4, C8, C10: 100n; C_1206_3216Metric_Pad1.33x1.80mm_HandSolder
C5, C6: 100u; C_1206_3216Metric_Pad1.33x1.80mm_HandSolder
C7, C9: 22u; C_1206_3216Metric_Pad1.33x1.80mm_HandSolder
D1, D2, D3, D4, D7, D8: LED; LED_0805_2012Metric_Pad1.15x1.40mm_HandSolder
D5: 1N4148W; D_SOD-123
D6: MBR1020VL; D_SOD-123F
F1: Fuse; Fuse_1812_4532Metric_Pad1.30x3.40mm_HandSolder
J1: Conn_01x03_Female; PinSocket_1x03_P2.54mm_Horizontal
J2: Conn_01x07_Female; Molex_Micro-Latch_53254-0770_1x07_P2.00mm_Horizontal
J3, J4, J5: Conn_01x02_Female; Molex_Micro-Latch_53254-0270_1x02_P2.00mm_Horizontal
K1: SANYOU_SRD_Form_C; Relay_SPDT_SANYOU_SRD_Series_Form_C
Q1, Q2: BSS138; SOT-23
Q4: BC548; TO-92_Inline
R1, R3, R4, R9, R10, R13: 10k; R_0603_1608Metric_Pad0.98x0.95mm_HandSolder
R2, R11, R12: 220; R_0603_1608Metric_Pad0.98x0.95mm_HandSolder
R5, R6, R7, R15, R19: 100k; R_0603_1608Metric_Pad0.98x0.95mm_HandSolder
R8: 330; R_0603_1608Metric_Pad0.98x0.95mm_HandSolder
R14: 1.2k; R_0603_1608Metric_Pad0.98x0.95mm_HandSolder
R16, R17: 1k; R_0603_1608Metric_Pad0.98x0.95mm_HandSolder
R18: 1.8k; R_0603_1608Metric_Pad0.98x0.95mm_HandSolder
RV1: 10k; Potentiometer_Bourns_3296W_Vertical
SW1: Program; SW_Push_SPST_NO_Alps_SKRK
SW2: ResetP; SW_Push_SPST_NO_Alps_SKRK
SW3: Reset; SW_Push_SPST_NO_Alps_SKRK
SW4: SW_DPDT_x2; SW_SPDT_CK-JS102011SAQN
U1: ESP32-WROOM-32
U2, U3: NHD-0420H1Z; LCD_LCD-20X4B
U4: PCF8574; PCF8574ADWR_DW16
U5: AMS1117-5.0; SOT-223-3_TabPin2
U6: AMS1117-3.3; SOT-223-3_TabPin2
U7: DMG3415U-7; SOT95P240X105-3N

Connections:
+3V3: C2.1, C9.1, C10.1, J2.7, Q1.1, Q2.1, R1.1, R9.2, R10.2, R13.1, SW3.1, U1.2, U6.2
+5V: C6.1, C7.1, C8.1, D5.1, K1.5, R3.1, R4.1, R8.1, R18.2, RV1.1, U2.2, U3.2, U4.16, U5.2, U6.3
+12V: C4.1, C5.1, K1.4, R17.1, SW4.3, U5.3
Crelay: R14.1, U1.12
GND: C1.2, C3.1, C4.2, C5.2, C6.2, C7.2, C8.2, C9.2, C10.2, D1.1, D2.1, D3.1, D7.1, D8.1, J1.3, J2.5, J3.2, J4.2, J5.2, Q4.3, R5.1, R6.1, R7.1, R15.2, R19.2, RV1.3, SW1.2, SW2.2, U1.1, U1.15, U1.38, U1.39, U2.1, U2.16, U3.1, U3.16, U4.8, U5.1, U6.1
unnamed: C1.1, R1.2, SW2.1, U1.3
unnamed: C2.2, SW3.2, U1.6
unnamed: C3.2, R13.2, SW1.1, U1.25
unnamed: D1.2, R2.1
unnamed: D2.2, R11.1
unnamed: D3.2, R12.1
unnamed: D4.1, D5.2, K1.2, Q4.1
unnamed: D4.2, R18.1
unnamed: D6.1, SW4.2, U7.2
unnamed: D6.2, F1.2, R15.1, R16.1, U7.1
unnamed: D7.2, R16.2
unnamed: D8.2, R17.2
unnamed: F1.1, J3.1
unnamed: J1.1, U1.35
unnamed: J1.2, U1.34
unnamed: J2.1, U1.29
unnamed: J2.2, U1.16
unnamed: J2.3, U1.37
unnamed: J2.4, U1.31
unnamed: J2.6, U1.28
unnamed: J5.1, K1.1
unnamed: Q1.3, R3.2, U4.14
unnamed: Q2.3, R4.2, U4.15
unnamed: Q4.2, R14.2, R19.1
unnamed: R2.2, U1.27
unnamed: R5.2, U4.1
unnamed: R6.2, U4.2
unnamed: R7.2, U4.3
unnamed: R8.2, U2.15, U3.15
unnamed: R11.2, U1.8
unnamed: R12.2, U1.9
unnamed: RV1.2, U2.3, U3.3
unnamed: U2.4, U3.4, U4.4
unnamed: U2.5, U3.5, U4.5
unnamed: U2.6, U3.6, U4.6
unnamed: U2.11, U3.11, U4.9
unnamed: U2.12, U3.12, U4.10
unnamed: U2.13, U3.13, U4.11
unnamed: U2.14, U3.14, U4.12
SCL: Q1.2, R9.1, U1.36
SDA: Q2.2, R10.1, U1.33
Vbat: J4.1, U7.3

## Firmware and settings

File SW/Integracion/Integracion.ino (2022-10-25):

#include <SPI.h>
#include <MFRC522.h>
// start of settings for LCD1602 with I2C
#include <LiquidCrystal_I2C.h>
// Set the LCD address to 0x27 for a 16 chars and 2 line display
LiquidCrystal_I2C lcd(0x27, 16, 4);
// watch video for details of 0x3F I2C address
// end of settings for LCD1602 with I2C
 #include<TimeLib.h> 
#define SS_PIN 25
#define RST_PIN 26
MFRC522 mfrc522(SS_PIN, RST_PIN);   // Create MFRC522 instance.
#include "BluetoothSerial.h"

#if !defined(CONFIG_BT_ENABLED) || !defined(CONFIG_BLUEDROID_ENABLED)
#error Bluetooth is not enabled! Please run `make menuconfig` to and enable it
#endif
int boton = 5;
int led1 = 2;
int led2 = 4;
BluetoothSerial SerialBT;
 
void setup() 
{
  Serial.begin(9600);   // Initiate a serial communication
  SerialBT.begin("ESP32");
  Serial.println("The device started, now you can pair it with bluetooth!");
  SPI.begin();      // Initiate  SPI bus
  mfrc522.PCD_Init();   // Initiate MFRC522
  lcd.init();  
  lcd.backlight();
  lcd.print("   LAB GEO-TECNIA  ");
  lcd.setCursor(0,1);
  lcd.print("ACERQUE SU TARJETA");  
  delay(2000); 
   pinMode(led1, OUTPUT);
  pinMode(led2, OUTPUT);
  pinMode(boton, OUTPUT);
  digitalWrite(led1, LOW);
  digitalWrite(led2, LOW);
    digitalWrite(boton, HIGH);
  
     
  Serial.println("Acerque su tarjeta");
  Serial.println();
    setTime(7,50,0,5,7,2022);

    
     

}
void loop() 

      {
   
  

  // Look for new cards
  if ( ! mfrc522.PICC_IsNewCardPresent()) 
  {
    return;
  }
  // Select one of the cards
  if ( ! mfrc522.PICC_ReadCardSerial()) 
  {
    return;
  }
  //Show UID on serial monitor
  Serial.print("UID tag :");
   SerialBT.print("UID tag :");
  String content= "";
  byte letter;
  for (byte i = 0; i < mfrc522.uid.size; i++) 
  {
     Serial.print(mfrc522.uid.uidByte[i] < 0x10 ? " 0" : " ");
     Serial.print(mfrc522.uid.uidByte[i], HEX);
      SerialBT.print(mfrc522.uid.uidByte[i] < 0x10 ? " 0" : " ");
     SerialBT.print(mfrc522.uid.uidByte[i], HEX);
     content.concat(String(mfrc522.uid.uidByte[i] < 0x10 ? " 0" : " "));
     content.concat(String(mfrc522.uid.uidByte[i], HEX));
  }
  Serial.println();
  Serial.print("Message : ");
  content.toUpperCase();
  if (content.substring(1) == "3E F4 72 51" || content.substring(1) == "08 B6 A9 43"  ) //change here the UID of the card/cards that you want to give access
  {
      
    Serial.println("Acceso autorizado");
     SerialBT.print(' ');
     SerialBT.println("Acceso autorizado");
         SerialBT.println();
 SerialBT.print("Fecha: ");
      SerialBT.print('\n');
 SerialBT.print (day(), DEC);
   SerialBT.print('/');
  SerialBT.print (month(), DEC);
    SerialBT.print('/');
   SerialBT.print(year(), DEC);
       SerialBT.print('\n');
     SerialBT.print("Hora: ");
      SerialBT.print('\n');
     SerialBT.print(hour(), DEC);
   SerialBT.print(':');
  SerialBT.print (minute(), DEC);
      SerialBT.print('\n');
      lcd.clear();
         lcd.setCursor(0,1);
  lcd.print("ACCESO AUTORIZADO");  
    Serial.println();
    digitalWrite(led2, HIGH);
    digitalWrite(led1, LOW);
    delay(3000);
           lcd.print("   LAB GEO-TECNIA  ");
     lcd.setCursor(0,1);
  lcd.print("ACERQUE SU TARJETA");
    digitalWrite(led2, LOW);
  }
 
 else   {
    Serial.println(" Acceso no autorizado");
    SerialBT.print(' ');
    SerialBT.println("Acceso no autorizado");
        SerialBT.println();
         SerialBT.print("Fecha: ");
      SerialBT.print('\n');
 SerialBT.print (day(), DEC);
   SerialBT.print('/');
  SerialBT.print (month(), DEC);
    SerialBT.print('/');
   SerialBT.print(year(), DEC);
       SerialBT.print('\n');
     SerialBT.print("Hora: ");
      SerialBT.print('\n');
     SerialBT.print(hour(), DEC);
   SerialBT.print(':');
  SerialBT.print (minute(), DEC);
      SerialBT.print('\n');;
        digitalWrite(led2, LOW);
        digitalWrite(led1, HIGH);
        lcd.clear();
           lcd.print("   LAB GEO-TECNIA  ");
              lcd.setCursor(0,1);
              
  lcd.print("ACCESO NO AUTORIZADO");
    delay(3000);
     lcd.setCursor(0,1);
  lcd.print("ACERQUE SU TARJETA");
    digitalWrite(led1, LOW);
  }
 
 void open_door() {

  lcd.setCursor (0, 3);//poner el cursor en las coordenadas (x,y)
  lcd.print("   Puerta Abierta!  ");//muestra en la pantalla max 20 caracteres
  delay(100);
  digitalWrite(signal_relay, HIGH);
  delay(40);
  digitalWrite(signal_relay, LOW);
  digitalWrite(led_open, HIGH);
  digitalWrite(led_close, LOW);
  delay(1500); //Tiempo desenergizado del iman
  digitalWrite(led_open, LOW);
  digitalWrite(led_close, HIGH);
  lcd.setCursor (0, 3);//poner el cursor en las coordenadas (x,y)
  lcd.print("   Puerta Cerrada!  ");//muestra en la pantalla max 20 caracteres
  delay(100);

}
}

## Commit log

2022-04-09 Por crear la carpeta
2022-04-28 Inicio Esquematico
    [SE.kicad_pcb, SE.sch]
2022-05-05 AJustes Dsiplay
    [SE.sch]
2022-05-05 Control REle y entrada sensnores
    [SE.sch]
2022-05-12 Primer diseño fuente
    [SE.sch]
2022-05-15 Esquematico Completo
    [Diplay.sch, Fuente-Bateria.sch, Rele.sch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]
2022-05-17 Ajustes Esquematico y Seleccion FootPrint
2022-05-17 Uso Flag de fuente
    [SE.sch]
2022-05-17 Correccion Esquematico
    [SE.sch]
2022-05-17 Asignacion FootPrint e inicio PCB
    [SE.kicad_pcb, SE.sch]
2022-05-24 Inicio PCB
    [SE.kicad_pcb, SE.sch]
2022-05-24 Ajuste PCB
    [SE.kicad_pcb]
2022-05-24 Distribucion final de componetes en 10*10
    [SE.kicad_pcb, SE.sch]
2022-05-24 Calculo pista 12V
    [SE.kicad_pcb]
2022-05-24 Conecciones Iniciales
    [SE.kicad_pcb]
2022-05-25 Ruteo y dimensionamiento
    [SE.kicad_pcb]
2022-05-25 PCB lista
    [SE.kicad_pcb]
2022-05-25 Nombramiento puertos y testigos
    [SE.kicad_pcb]
2022-05-27 Ajustes Finales PCB
    [SE-B_Cu.gbr, SE-B_Mask.gbr, SE-B_Paste.gbr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]
2022-05-31 Dimensiones agujeros de agarre PCB
    [SE.kicad_pcb]
2022-07-05 Proceso de Compra
2022-07-06 Diagrama de bloques
2022-07-06 Diagrama de Flujo
